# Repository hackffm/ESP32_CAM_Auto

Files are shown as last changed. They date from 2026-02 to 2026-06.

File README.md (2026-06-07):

# ESP32_CAM_Auto
ESP32 Camera FPV Car - some description also on our [Hackerspace-FFM e.V. FPV-Roboter page](https://www.hackerspace-ffm.de/wiki/index.php?title=FPV-Roboter)

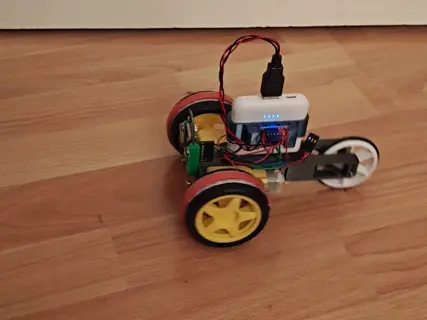
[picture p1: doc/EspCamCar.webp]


# Software setup
## Initial programming of ESP32 CAM Module
Connect it to USB-Serial-Board, hit `Pioarduino -> Project Tasks -> esp32cam -> Custom -> Initial Erase + Flash + FS + Monitor`. 

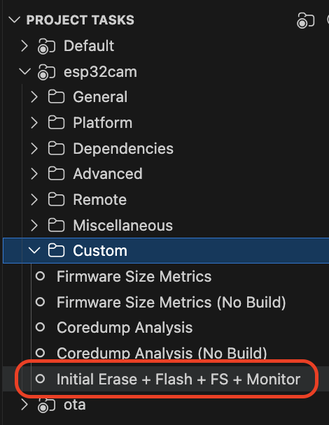
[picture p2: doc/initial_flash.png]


## Architecture infos
- LittleFS is used to store and retrieve WiFi credentials, botname and motor configs. This usually survives a FW update if LittleFS is not uploaded as well. Defaults are used, but LittleFS must be initialized. 
- Camera streams over http port 81 in MJPG mode - this guarantees lowest latency as next frame is only tranferred if current frame was delivered. Usually no significant buffering is used in browsers (this is different for eg RTSP that is why it is not used)
- Code is optimized for OV3660 cameras and support OV2640 cameras. ESP32 CAM boards have known issues with extreme WiFi lag due EMI issues with camera clock signal. We are using the following trick: Reduce external camera clock from 20Mhz to 8Mhz, but then using camera interanl PLL to get same speed again, that way we face much less interference issues.
- http deliveres index.htm and info and action point on port 80. Info streams every second info to browser like fps, but also names for sliders. action is used for controlling everything that is send from browser to the ESP (steering but also settings).
- pwmThing class encapsulates all PWM actions to control LED brightness, set motor speed and servo positions.
- Care must be taken that PWM stuff like analogWrite usually used high-speed timers, but camera clock is using low-speed timers. Arduino does not know about the already used camera timers, but as it uses high-speed timers instead there is no conflict.

# Hardware setup
## Cabling with special PCB
With the special PCB cabling is as easy as connecting left and right motor to the upper 2pin row of the headers and the servo to the lower 3pin row of the headers. For servo, the control line (typical the yellow cable) goes to where the pin is missing on the row above.
If servo does not work, you might need to turn the connector - as long as all 3 pins are connected nothing should broke even if the connector is in the wrong direction. For motor, check that the motors turn forward if you control the joystick forward, otherwise just turn the 2pin connector to change the motor direction of that motor that rotates in the wrong direction.

Supply power from Power Bank via USB-C cable to PCB to turn on the robot. Beware that the PCB does not include the programming hardware for the ESP-CAM - you have to program the ESP-CAM module with a separate programming adapter and then transfer it to the motor driver PCB.

PCB preparation: The idea is that you cut Pin 1 (the one with the square pad on the PCB) away to get a 3+2 pol connector from that originally 2x3 pol connector.
## Manual cabling
- For full-bridge motor drivers connect inputs to 12+13 and 15+14, add connectors to the motors that you can easily swap or turn the motor lines to adjust for correct drive direction
- For 360° servos just pick two of the available pins and set them up via web interface for left and right motor
- We used an USB A plug and a power supply for suppy. In such a case wire separate cables for motors and for ESP32 beginning from USB plug to avoid issues that motor starting currents are affecting ESP32

See the following picture how we did it:

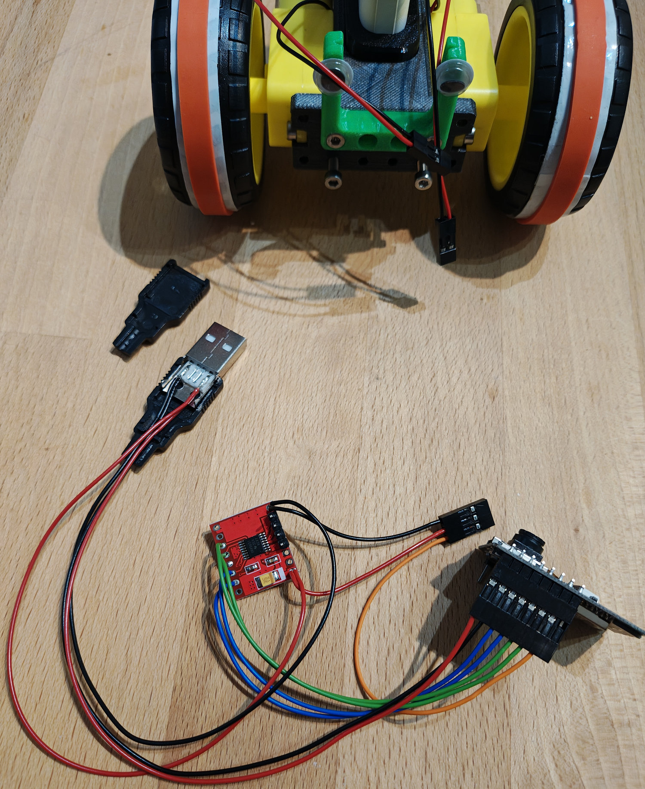
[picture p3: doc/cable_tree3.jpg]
cabling1


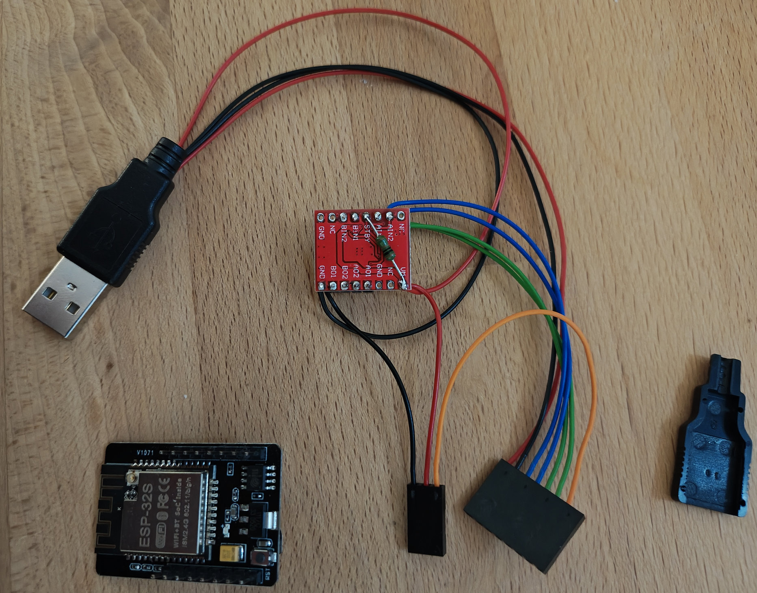
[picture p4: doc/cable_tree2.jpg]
cabling2


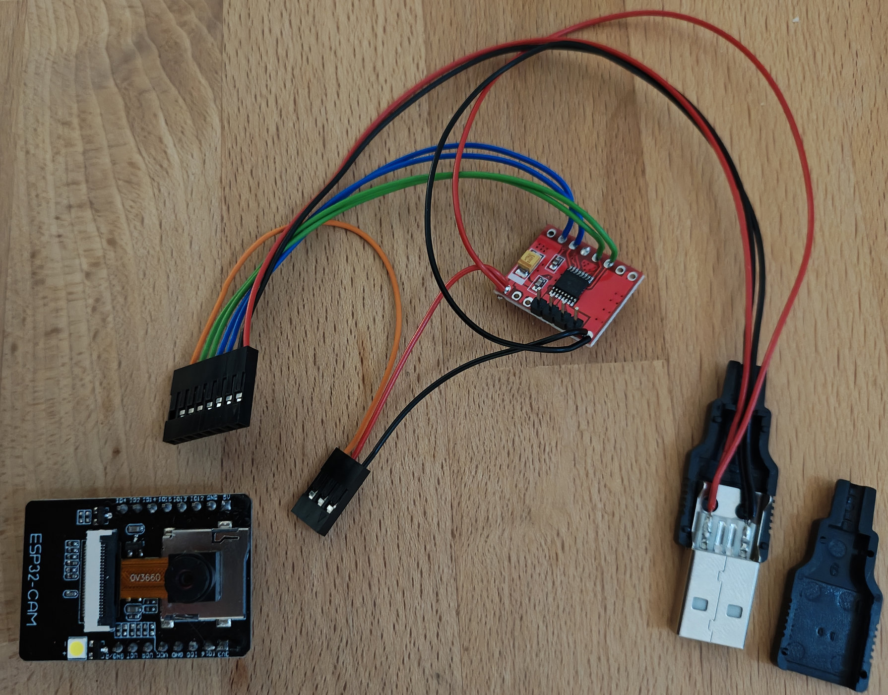
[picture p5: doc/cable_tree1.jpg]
cabling3


## Usable pins
Pins can be redefined via Webinterface but on ESP32 CAM only the following pins are selectable and usable: 
- -1 (if pin or function not needed)
- 2, 12, 13, 14, 15 (free for use, SD card can not be used as these are also for SD card)
- 3 (if used, serial RX is not available anymore)

The following pins can not be used even if they are available on the ESP32 CAM board:
- 0 is used for camera clock signal
- 16 is internally used for PSRAM
- 1 is used for serial TX
- 4 is controlling the white flash LED
- 33 is controlling the red internal LED (might be usable if RedLed PWMThing is connected to pin -1)

## Supported motors
Both servos and full-bridge motor drivers are supported. Currently only seperate left- and right-motor are supported (no steering servo). Servos can then be 360deg servos used as motors, adjust min/zero/max limits for servos, zero is where 360deg servos does not turn (but they are stopped if appropriate servo variant is selected anyway).

# Usage
## LED indications
Slow breathing red LED means normal operation and having a valid WiFi connection. You should be able to control your robot via website of the IP or the name the robot (default: http://cambot.local)

Fast breathing red LED means robot has not found a valid WiFi connection and is acting as WiFi access point. Scan you WiFi environment, connect to the WiFi that matches your robot name (default: cambot), and then go to http://192.168.4.1 to either control your robot directly or connect it to your home WiFi using the Settings area, where you could also scan for your WiFi access points. Beware that the ESP-CAM is 2.4GHz only, so you can connect it only access points that support 2.4GHz WiFi.

No breathing or blinking or off: Something is broken or not powered. If white LED blinks two times the modul could not start the camera module - so check the connection to the camera module first. Beware that to open the camera connector you have to twist the black element by 90° (meaning pulling it away from PCB surface) and not pull it along the PCB. Currently supported camera modules: OV2640 or OV3660 (recommended).

# Known issues
## It does not compile
Uninstall ESP32 core modules in Platform-IO first to force installing newest ones.

### This versions gave a running config
PACKAGES: 
 - contrib-piohome @ 3.4.4 
 - framework-arduinoespressif32 @ 3.3.7 
 - framework-arduinoespressif32-libs @ 5.5.0+sha.87912cd291 
 - tool-esp-rom-elfs @ 2024.10.11 
 - tool-esptoolpy @ 5.1.2 
 - toolchain-xtensa-esp-elf @ 14.2.0+20251107

## Connection issues
- Check Serial output for IP address and if Wifi connection worked.
- Most browsers need at least a slash at the end to not trigger the search engine, try `cambot/`first.
- Name server often have issues, mDNS is also active, try `cambot.local/`if IP can not be resolved.
- Some browsers tries always https, but only http is supported now, try `http://cambot.local`in such case.
- Last resort enter ip address in browser
- If WiFi credentials are not set, either set them via Serial terminal or connect to access point of the device, then open `http://192.168.4.1/`and set there Wifi SSID + password, then power cycle.

## FPS 
Ok, you want the picture as smooth as possible, why limit FPS then? If WiFi is too much congested, everything starts getting sluggy, especially if more than one FPV car is operated it can make sense to limit the frame rate to leave some room for other players. WiFi at 2.4 GHz can transmit around 3,000 kBytes/s (but an ESP32 max out usually already at 1,000 kBytes/s due internal limits), depending on quality settings and picture size we integrated at least 4 fpv cars in the band without issues simultaneously. Keep an eye on RSSI, if it falls below -70 dBm the WiFi bandwith starts to be limited significantly affecting also the frame rate of that vehicle.  

## Camera overheating
Especially the OV3660 moduls are working on ESP32 CAM boards, but are operated out of voltage specifications there. Therefore they are more prone to heat up - glue them with thin double sided tape to the SD card holder to give them a little more cooling surface. Camera is specified to operate with best picture quality up to 50°C, they are specified to allow operation up to 70°C, we see it often a little bit higher than that but it seems to be ok. As said, issue is that OV2640 is usually prefered over OV3660 du to better picture and speed but are more prone to overheating.

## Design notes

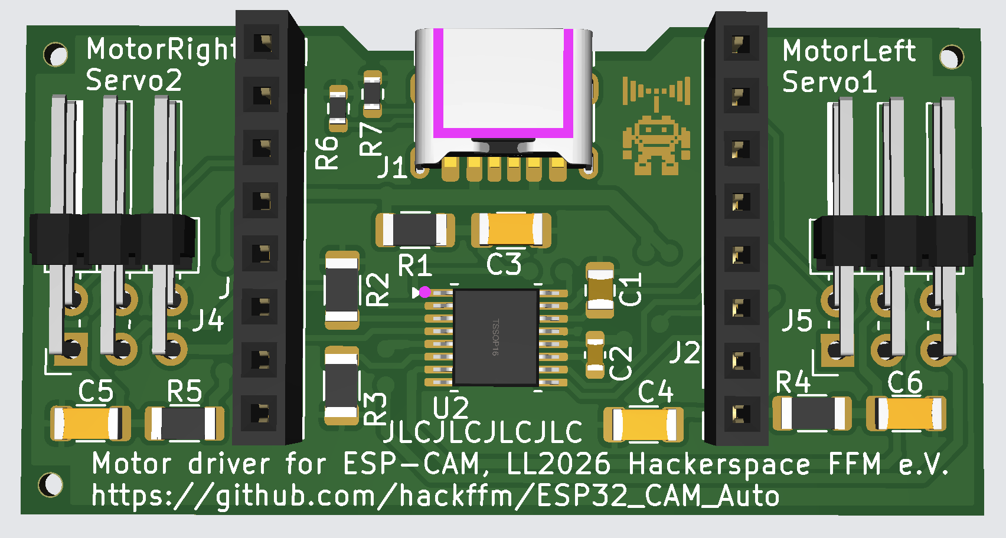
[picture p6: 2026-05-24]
pcb/docu/Motor driver for ESP-CAM PCB 3D.png

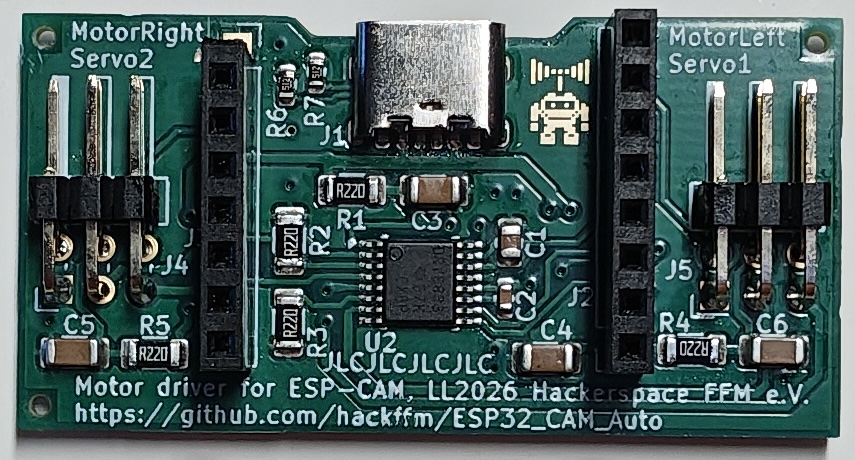
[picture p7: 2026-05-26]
pcb/docu/Motor driver PCB delivered and pins cut.jpg

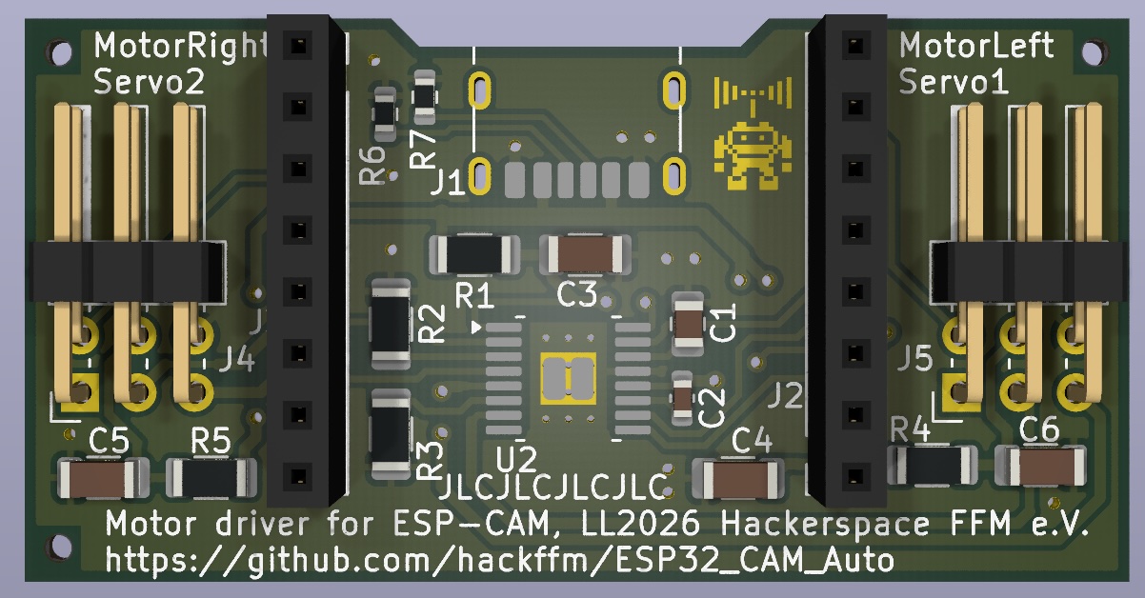
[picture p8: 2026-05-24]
pcb/docu/Motor driver for ESP-CAM KiCadRendering.jpg

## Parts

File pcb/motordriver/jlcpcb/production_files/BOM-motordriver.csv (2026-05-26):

Comment | Designator | Footprint | LCSC | Quantity
0.01uF | C2 | C_0603_1608Metric | C57112 | 1
0.22R | R1,R2,R3,R4,R5 | R_1206_3216Metric | C327006 | 5
2.2uF | C1 | C_0805_2012Metric | C377773 | 1
22uF | C3,C4,C5,C6 | C_1206_3216Metric | C12891 | 4
5k1 | R6,R7 | R_0603_1608Metric | C23186 | 2
Conn_01x08_Pin | J2,J3 | PinSocket_1x08_P2.54mm_Vertical | C22438158 | 2
Conn_02x03_Odd_Even | J4,J5 | PinHeader_2x03_P2.54mm_Horizontal | C492431 | 2
DRV8833PWP | U2 | HTSSOP-16-1EP_4.4x5mm_P0.65mm_EP3.4x5mm_Mask2.46x2.31mm_ThermalVias | C50506 | 1
USB_C_Receptacle_PowerOnly_6P | J1 | USB_C_Receptacle_HRO_TYPE-C-31-M-17 | C283540 | 1
~ | H3 | Hole_Tooling_JLCPCB |  | 1
~ | H2 | Hole_Tooling_JLCPCB |  | 1
~ | H1 | Hole_Tooling_JLCPCB |  | 1
~ | PN1 | Part_Num_JLCPCB |  | 1

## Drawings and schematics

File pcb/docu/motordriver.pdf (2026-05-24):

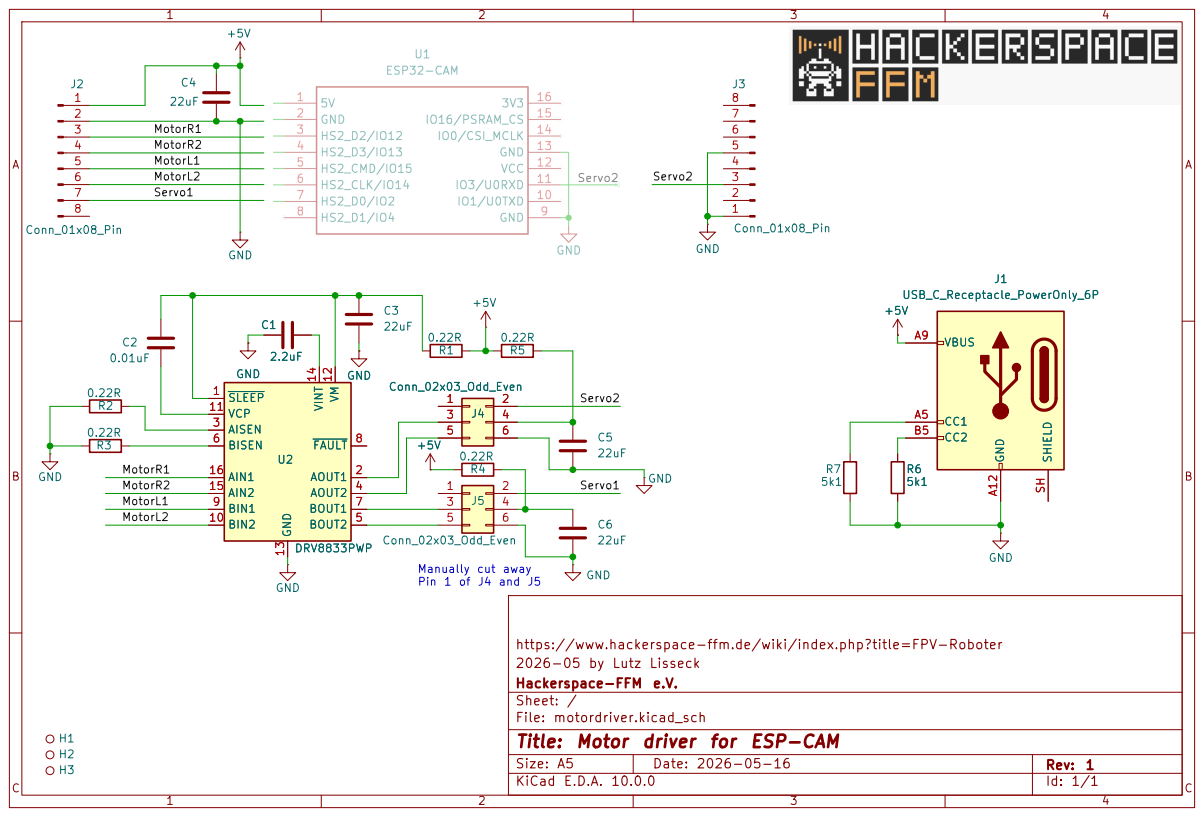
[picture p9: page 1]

Servo1 Manually cut away Pin 1 of J4 and J5 +5V

Sheet: /
File: motordriver.kicad_sch
Title: Motor driver for ESP-CAM

Size: A5 | Rev: 1 | C Date: 2026-05-16 KiCad E.D.A. 10.0.0

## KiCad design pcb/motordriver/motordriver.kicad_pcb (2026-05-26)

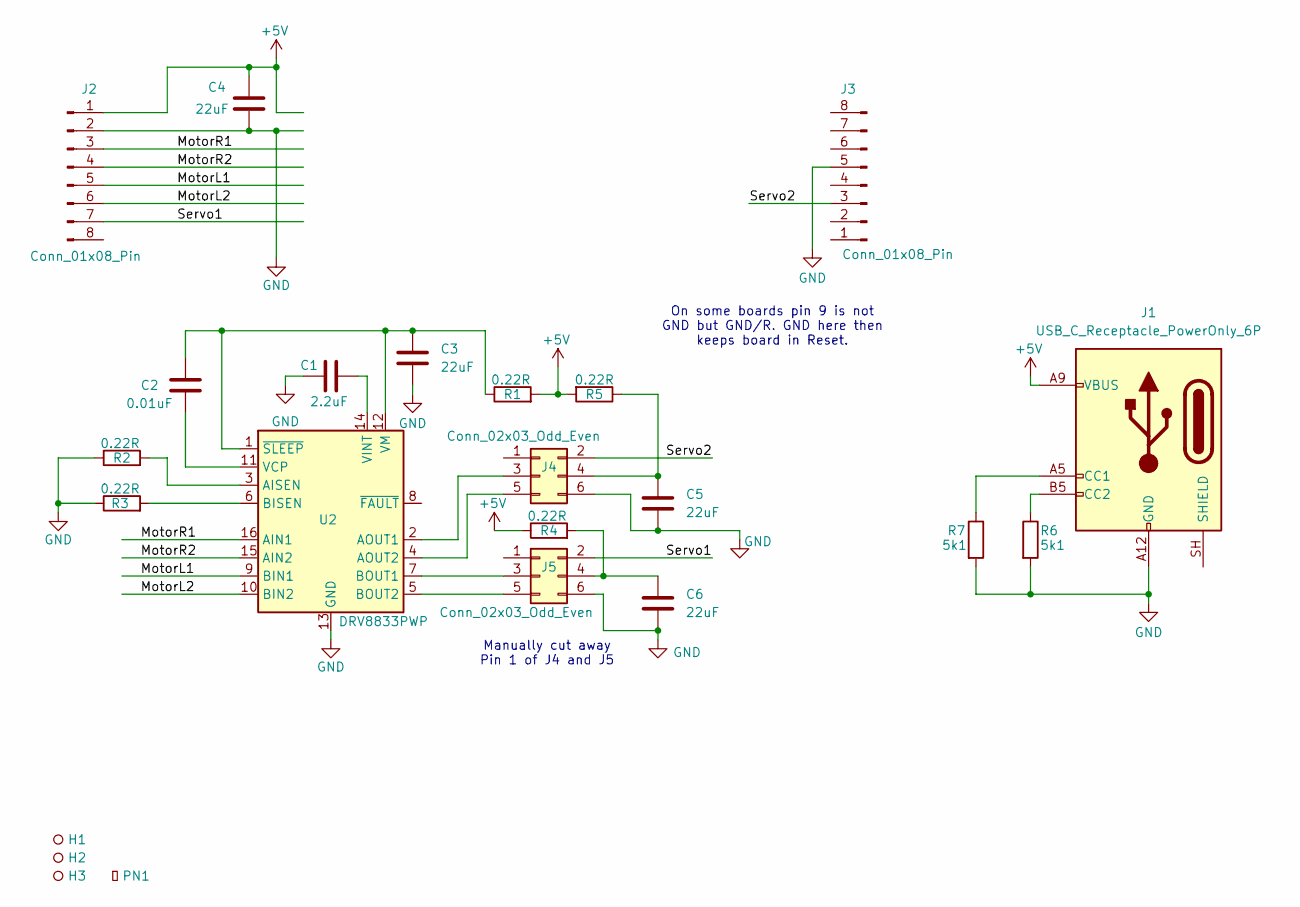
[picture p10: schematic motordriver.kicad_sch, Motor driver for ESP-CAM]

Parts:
C1: 2.2uF; C_0805_2012Metric; LCSC C377773
C2: 0.01uF; C_0603_1608Metric; LCSC C57112
C3, C4, C5, C6: 22uF; C_1206_3216Metric; LCSC C12891
H1, H2, H3: Hole_Tooling_JLCPCB
J1: USB_C_Receptacle_PowerOnly_6P; USB_C_Receptacle_HRO_TYPE-C-31-M-17; LCSC C283540
J2, J3: Conn_01x08_Pin; PinSocket_1x08_P2.54mm_Vertical; LCSC C22438158
J4, J5: Conn_02x03_Odd_Even; PinHeader_2x03_P2.54mm_Horizontal; LCSC C492431
PN1: Part_Num_JLCPCB
R1, R2, R3, R4, R5: 0.22R; R_1206_3216Metric; LCSC C327006
R6, R7: 5k1; R_0603_1608Metric; LCSC C23186
U2: DRV8833PWP; HTSSOP-16-1EP_4.4x5mm_P0.65mm_EP3.4x5mm_Mask2.46x2.31mm_The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; LCSC C50506

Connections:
+5V: C4.2, J1.A9 (VBUS), J1.B9 (VBUS), J2.1, R1.2, R4.1, R5.2
/MotorL1: J2.5, U2.9 (BIN1)
/MotorL2: J2.6, U2.10 (BIN2)
/MotorR1: J2.3, U2.16 (AIN1)
/MotorR2: J2.4, U2.15 (AIN2)
/Servo1: J2.7, J5.2
/Servo2: J3.3, J4.2
GND: C1.1, C3.2, C4.1, C5.2, C6.2, J1.A12 (GND), J1.B12 (GND), J2.2, J3.5, J4.6, J5.6, R2.1, R3.1, R6.2, R7.2, U2.13 (GND), U2.17 (GND)
unnamed: J1.A5 (CC1), R7.1
unnamed: J1.B5 (CC2), R6.1
unnamed: J4.3, U2.2 (AOUT1)
unnamed: C5.1, J4.4, R5.1
unnamed: J4.5, U2.4 (AOUT2)
unnamed: J5.3, U2.7 (BOUT1)
unnamed: C6.1, J5.4, R4.2
unnamed: J5.5, U2.5 (BOUT2)
unnamed: R2.2, U2.3 (AISEN)
unnamed: R3.2, U2.6 (BISEN)
unnamed: C2.2, U2.11 (VCP)
unnamed: C1.2, U2.14 (VINT)
unnamed: C2.1, C3.1, R1.1, U2.1 (~SLEEP), U2.12 (VM)

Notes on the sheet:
Manually cut away Pin 1 of J4 and J5
On some boards pin 9 is not GND but GND/R. GND here then keeps board in Reset.

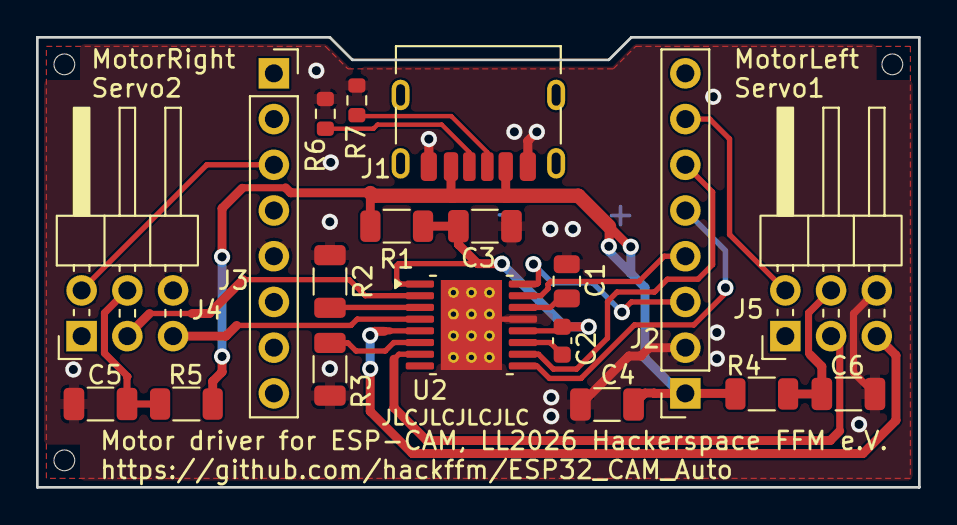
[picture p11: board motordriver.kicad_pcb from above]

Board: 2 copper layers, 49.0 x 25.0 mm, 23 parts (0 on the bottom side), 21 nets.

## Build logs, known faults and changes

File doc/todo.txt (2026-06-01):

Webseite:
  - SSID (Wlan-Name hinterschreiben weil leute SSID nicht wissen)
  - Übernamhme der Daten mit Reboot wurde nicht verstanden 
    - wie drücken oder ab- neu anstecken
  - Servo-Button ins Bild
  - Controller Settings speichern (im Browser speichern)
  - Manuelle Controller Auswahl broken
  - 7fps muss weg 
  - Bild 180 drehen

Anleitung:
  - Wie Wifi Einstellungen prüfen (Verbindung geht oder noch im AP Modus)
  - Hinweis das Wifi-Passwort aufs Handy zu übertragen bevor auf den Bot-AP gewechselt wird
  - 5Ghz only geht nicht  
  
Wifi:
  - Captive Portal Seite ging nicht (WLED checken)
  - Erkannte APs zur Auswahl anzeigen

Auto-Power-Down nach Inaktivität

FW Update

Extra Einstellungen:
- Bild 180 drehen
-

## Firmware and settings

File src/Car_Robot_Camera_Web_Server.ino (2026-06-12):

/*********
 
   The MIT License (MIT) 
   Hackerspace-FFM e.V. ESP32 CAM Robot with Web Interface
   https://www.hackerspace-ffm.de/wiki/index.php?title=FPV-Roboter
   2026-06-12 Lutz Lisseck 

  Derived from this work: 
  Rui Santos & Sara Santos - Random Nerd Tutorials
  Complete instructions at https://RandomNerdTutorials.com/esp32-cam-projects-ebook/
  Permission is hereby granted, free of charge, to any person obtaining a copy of this software and associated documentation files.
  The above copyright notice and this permission notice shall be included in all copies or substantial portions of the Software.
*********/

const char version_string[] = "V1.14";

#define MOTOR_1_PIN_1    14
#define MOTOR_1_PIN_2    15
#define MOTOR_2_PIN_1    13
#define MOTOR_2_PIN_2    12
#define SERVO_1_PIN       2
#define WHITE_LED_PIN     4
#define RED_LED_PIN      33

// Wifi credentials are in a MyCreds.h file that must reside in /<HOME>/.platformio/lib/MyCreds/MyCreds.h
// see attic/MyCreds.h for an example
#if defined __has_include
#  if __has_include (<MyCredsLabyrinth.h>)
#    include <MyCredsLabyrinth.h>  // Define WIFI_SSID and WIFI_PASSWORD here - put this file in /<HOME>/.platformio/lib/MyCreds/MyCredsHackffm.h
#  else
#    define WIFI_SSID ""
#    define WIFI_PASSWORD ""
#  endif
#else
#  define WIFI_SSID ""
#  define WIFI_PASSWORD ""
#endif

// Replace with your network credentials, will be overwritten by values stored in LittleFS if available
char roboter_name[34] = "cambot"; // only use a-z, 0-9 and - in the name 
char wifi_ssid[34] = WIFI_SSID;  // "REPLACE_WITH_YOUR_SSID";
char wifi_password[66] = WIFI_PASSWORD; // "REPLACE_WITH_YOUR_PASSWORD";

// =============================================================
//  User-configurable channel list for scanning.
//  Fill this with the channels you actually want to probe.
//  Using non-overlapping channels (e.g. 1, 6, 11 or 1, 7, 13)
//  keeps the scan short and the stream interruption minimal.
//  Leave empty {} to scan ALL channels (slower).
// =============================================================
static const uint8_t ROAM_SCAN_CHANNELS[] = {}; //{1,2,3,4,5,6,7,8,9,10,11,12,13}; // { 1, 7, 13 };
static const size_t  ROAM_SCAN_CHANNEL_COUNT =
        sizeof(ROAM_SCAN_CHANNELS) / sizeof(ROAM_SCAN_CHANNELS[0]);

#include "esp_camera.h"
#include <WiFi.h>
#include "esp_wifi.h"
#include <WiFiMulti.h>
#include <WiFiUdp.h>
#include <lwip/sockets.h>
#include <lwip/netdb.h>
#include <DNSServer.h> // For captive portal
#include <ESPmDNS.h>
#include "esp_timer.h"
#include "img_converters.h"
#include "Arduino.h"
#include "fb_gfx.h"
#include "soc/soc.h"             // disable brownout problems
#include "soc/rtc_cntl_reg.h"    // disable brownout problems
#include "esp_http_server.h"
#include "driver/ledc.h" 
#include <ArduinoOTA.h>
#include "PwmThing.h"
#include "FS.h"
#include <LittleFS.h> 
#include <string.h>
#include <stdlib.h>
#include <ctype.h>

// =============================================================
//  Detect whether 802.11r Fast Transition is compiled into
//  this build. This is decided at compile time.
// =============================================================
#ifdef CONFIG_ESP_WIFI_11R_SUPPORT
  #define ROAM_FT_AVAILABLE 1
#else
  #define ROAM_FT_AVAILABLE 0
#endif

#define ENABLE_OTA 
int OTA_Status = 0; // 0=not enabled, 1=enabled, 2=in progress
DNSServer dnsServer;
bool APMode = false;
bool RoamForceTriggered = false;


IPAddress current_IP(192, 168, 4, 1);
char      current_ssid[34] = ""; 
char      current_bssid[34] = ""; 
int       current_channel = 0;
int       current_rssi = -50;

PwmThing MotorLeft, MotorRight, Servo1, Servo2, WhiteLED, RedLED;

WiFiMulti wifiMulti;

// Gamemaster stuff
const unsigned int gmPort = 8071;        // UDP port for gamemaster
IPAddress gmLastRemoteIp;
uint16_t  gmLastRemotePort = 0;
bool      gmLastRemoteValid = false;
WiFiUDP gmUdp;

// Store data used in PwmThing.begin for Motors and Servos here in an array of a structto be stored in LittleFS and to be used on startup
struct PwmThingConfig {
  char name[20]; int pinA; int pinB; PwmThing::ThingType thingType; bool inverted;
  int servoMin; int servoZero; int servoMax; /* Only for servos*/
};

// Create an array of PwmThingConfig for the motors and servos and populate it with default values
const int numPwmThings = 4;
PwmThingConfig pwmThingConfigs[numPwmThings] = {
  {"MotorLeft", MOTOR_1_PIN_1, MOTOR_1_PIN_2, PwmThing::halfBridgeIdleHigh, false, 768, 4760, 9544},
  {"MotorRight", MOTOR_2_PIN_1, MOTOR_2_PIN_2, PwmThing::halfBridgeIdleHigh, false, 768, 4760, 9544},
  {"Servo1", SERVO_1_PIN, -1, PwmThing::servoMotor, false, 768, 4760, 9544},
  {"Servo2", -1, -1, PwmThing::servoMotor, false, 768, 4760, 9544}
};

uint32_t lastMotorCommandTime = 0;
uint32_t powerDownTimer = 0;
uint32_t powerDownTimeout = 60 * 60000UL; // Power down 30 min

struct LightVariables {
  // All values are usually 0...255 for 0% to 100% brightness
  int requestedValue = -1;          // User request goes here, -1 means no request, applied in main loop with limits and timeouts
  int Value = 0;                    // What the light is currently set to, timeouts and limits are applied to this value, and this is what is actually set on the LED
  int lowValue = 50;                // User defined value for candle/torch light (no time limit if below limitLowValue)
  int highValue = 255;              // User defined value for strong brightness (will be time limited)
  int limitLowValue = 75;           // Unlimited brightness up to this value, above this value, the timeout will apply
  int limitHighValue = 250;         // Absolute maximum allowed brightness, even for boost, to prevent overheating
  int boostTime = 30000;            // Available boost time in milliseconds
  int boostTimeMax = 30000;         // Maximum boost time in milliseconds (e.g. to calculate remaining boost time percentage)
} LightVars;

struct ServoVariables {
  // All values -255 ... 255 typically (percentage of PwmThing ServoMin and ServoMax)
  int requestedValue = -9999;    // User request goes here, -9999 means no request, applied in main loop with limits and timeouts
  int Value = 0;                 // What the servo is currently set to
  int lowValue = -30;            // User defined value for one lower position 
  int highValue = 150;           // User defined value for one higher position
} Servo1Vars, Servo2Vars;

#define CAMERA_MODEL_AI_THINKER
//#define CAMERA_MODEL_M5STACK_PSRAM
//#define CAMERA_MODEL_M5STACK_WITHOUT_PSRAM
//#define CAMERA_MODEL_M5STACK_PSRAM_B
//#define CAMERA_MODEL_WROVER_KIT

#include "cam_pindefs.h"
#include "cam_streamhandler.h"
#include "indexhtml_intern.h"  // will be replaced if /data/index.html in LittleFS exists
#include "settingshtml_intern.h"  // will be replaced if /data/settings.html in LittleFS exists

#include "helper_functions.h"

struct CameraConfig {
  int rotation; // 0 = no rotation, 1 = 180° rotation
  int size; // 0 = 320x240 (QVGA), 1 = 400x296 (CIF), 2 = 640x480 (VGA), 3 = 800x600 (SVGA), 4 = 1024x768 (XGA), 5 = 1280x1024 (SXGA), 6 = 1600x1200 (UXGA)
  int fps; // Limit FPS, 0 = auto, 1...7 = 2,5,10,15,20,25,30 fps
  int quality; // 0 = auto, 1 very poor (63), 2 poor (42), 3 medium (30), 4 good (18), 5 very good (6)
} cameraConfig = {0, 2, 0, 0};
// current values go to quality and frame_limit_ms in cam_streamhandler.h, they are updated from there when changed 

fs::FS &filesystem = LittleFS;

void setCameraToConfig() {
  sensor_t * s = esp_camera_sensor_get();
  framesize_t size2framesize[] = {FRAMESIZE_QVGA, FRAMESIZE_CIF, FRAMESIZE_VGA, FRAMESIZE_SVGA, 
    FRAMESIZE_XGA, FRAMESIZE_SXGA, FRAMESIZE_UXGA};
  if(cameraConfig.size < 0 || cameraConfig.size > 6) cameraConfig.size = 2; // default to VGA if out of bounds  
  s->set_framesize(s, size2framesize[cameraConfig.size]);
  //s->set_quality(s, cameraConfig.quality);

  int fps_values[] = {15, 2, 5, 10, 15, 20, 25, 30};
  if(cameraConfig.fps < 0 || cameraConfig.fps > 7) cameraConfig.fps = 0; // default to auto if out of bounds
  int fps_value = fps_values[cameraConfig.fps];
  frame_limit_ms = fps_value > 0 ? 1000 / fps_value : 0; // 0 means no limit

  int quality_values[] = {33, 63, 42, 30, 18, 6}; // Map 0...5 to quality values (0=auto, 1=very poor, ..., 5=very good)
  if(cameraConfig.quality < 0 || cameraConfig.quality > 5) cameraConfig.quality = 0; // default to auto if out of bounds
  quality = quality_values[cameraConfig.quality];

  camera_sensor_info_t *info = esp_camera_sensor_get_info(&s->id);

  if((info->model == CAMERA_OV3660)) {
    if(cameraConfig.rotation == 1) {
      s->set_hmirror(s, 0);
      s->set_vflip(s, 1);
    } else {
      s->set_hmirror(s, 1);
      s->set_vflip(s, 0);
    }
    //s->set_xclk(s, LEDC_TIMER_0, 8000000UL);
    s->set_pll(s, 0, 25, 1, 0, 0, 0, 1, 10); // pushes 8MHz ext to same internally as 20mhz before
    s->set_reg(s, 0x302c, 0xc0, 0x00); // Reduce pad driving strength for better EMI/radio 
    s->set_reg(s, 0x6706, 0x0f, 0x03); // Adjust temperature sampling frequency to 8 MHz XVCLK
    // s->set_brightness(s, 0); // Increase brightness to reduce noise in dark areas
    //s->set_raw_gma(s, 1); s->set_reg(s, 0x5480, 1, 0);
    //s->set_gainceiling(s, GAINCEILING_32X);
  } else if(s->id.PID == OV2640_PID) {
    if(cameraConfig.rotation == 1) {
      s->set_hmirror(s, 1);
      s->set_vflip(s, 1);
    } else {
      s->set_hmirror(s, 0);
      s->set_vflip(s, 0);
    }
    s->set_gainceiling(s, (gainceiling_t)2); // default is 2x, set to 1x to reduce noise
    s->set_reg(s, 0x111, 0xff, 0x80); // activae clock doubler to compensate 8 Mhz 
  }

}

void storeCameraConfig() {
  char buffer[50];
  snprintf(buffer, sizeof(buffer), "%d,%d,%d,%d\n", cameraConfig.rotation, cameraConfig.size, cameraConfig.fps, cameraConfig.quality);
  writeFile("/camera_config.txt", buffer);
}

void loadCameraConfig() {
  char buffer[50];
  if(filesystem.exists("/camera_config.txt")) {
    File file = filesystem.open("/camera_config.txt", "r");
    if(file) {
      size_t len = file.readBytes(buffer, sizeof(buffer)-1);
      buffer[len] = '\0';
      sscanf(buffer, "%d,%d,%d,%d", &cameraConfig.rotation, &cameraConfig.size, &cameraConfig.fps, &cameraConfig.quality);
      file.close();
    }
  }
}

void initPwmThings() {
    // Disable UART RX if pinA or pinB is using GPIO3
    if(pwmThingConfigs[0].pinA == 3 || pwmThingConfigs[0].pinB == 3 || 
       pwmThingConfigs[1].pinA == 3 || pwmThingConfigs[1].pinB == 3 || 
       pwmThingConfigs[2].pinA == 3 || pwmThingConfigs[2].pinB == 3 || 
       pwmThingConfigs[3].pinA == 3 || pwmThingConfigs[3].pinB == 3) {
      Serial.println("Disabling UART RX because GPIO3 is used for IO.");
      delay(100); Serial.end();
      Serial.begin(115200, SERIAL_8N1, -1); // Disable RX pin by setting it to -1
    }
    MotorLeft.begin(pwmThingConfigs[0].pinA, pwmThingConfigs[0].pinB, pwmThingConfigs[0].thingType, pwmThingConfigs[0].inverted, 
      pwmThingConfigs[0].servoMin, pwmThingConfigs[0].servoZero, pwmThingConfigs[0].servoMax);
    MotorRight.begin(pwmThingConfigs[1].pinA, pwmThingConfigs[1].pinB, pwmThingConfigs[1].thingType, pwmThingConfigs[1].inverted,
      pwmThingConfigs[1].servoMin, pwmThingConfigs[1].servoZero, pwmThingConfigs[1].servoMax);
    Servo1.begin(pwmThingConfigs[2].pinA, pwmThingConfigs[2].pinB, pwmThingConfigs[2].thingType, pwmThingConfigs[2].inverted,
      pwmThingConfigs[2].servoMin, pwmThingConfigs[2].servoZero, pwmThingConfigs[2].servoMax);
    Servo2.begin(pwmThingConfigs[3].pinA, pwmThingConfigs[3].pinB, pwmThingConfigs[3].thingType, pwmThingConfigs[3].inverted,
      pwmThingConfigs[3].servoMin, pwmThingConfigs[3].servoZero, pwmThingConfigs[3].servoMax);
}

void storePwmThingConfigs() {
  char filename[30];
  char buffer[256];
  for(int i=0; i<numPwmThings; i++) {
    snprintf(filename, sizeof(filename), "/%s.txt", pwmThingConfigs[i].name);
    snprintf(buffer, sizeof(buffer), "%d,%d,%d,%d,%d,%d,%d\n", 
      pwmThingConfigs[i].pinA, pwmThingConfigs[i].pinB, (int)pwmThingConfigs[i].thingType, (int)pwmThingConfigs[i].inverted,
      pwmThingConfigs[i].servoMin, pwmThingConfigs[i].servoZero, pwmThingConfigs[i].servoMax);
    writeFile(filename, buffer);
  }
}

void loadPwmThingConfigs() {
  char filename[30];
  char buffer[256];
  for(int i=0; i<numPwmThings; i++) {
    snprintf(filename, sizeof(filename), "/%s.txt", pwmThingConfigs[i].name);
    if(filesystem.exists(filename)) {
      File file = filesystem.open(filename, "r");
      if(file) {
        size_t len = file.readBytes(buffer, sizeof(buffer)-1);
        buffer[len] = '\0';
        sscanf(buffer, "%d,%d,%d,%d,%d,%d,%d", 
          &pwmThingConfigs[i].pinA, &pwmThingConfigs[i].pinB, (int*)&pwmThingConfigs[i].thingType, (int*)&pwmThingConfigs[i].inverted,
          &pwmThingConfigs[i].servoMin, &pwmThingConfigs[i].servoZero, &pwmThingConfigs[i].servoMax);
        file.close();
      }
    }
  }
}

void loadLightServoLowHighVals() {
  char buffer[50];
  if(filesystem.exists("/ls_lh_vals.txt")) {
    File file = filesystem.open("/ls_lh_vals.txt", "r");
    if(file) {
      size_t len = file.readBytes(buffer, sizeof(buffer)-1);
      buffer[len] = '\0';
      sscanf(buffer, "%d,%d,%d,%d,%d,%d", &LightVars.lowValue, &LightVars.highValue, &Servo1Vars.lowValue, &Servo1Vars.highValue, &Servo2Vars.lowValue, &Servo2Vars.highValue);
      file.close();
    }
  }
}

void storeLightServoLowHighVals() {
  char buffer[50];
  snprintf(buffer, sizeof(buffer), "%d,%d,%d,%d,%d,%d\n", LightVars.lowValue, LightVars.highValue, Servo1Vars.lowValue, Servo1Vars.highValue, Servo2Vars.lowValue, Servo2Vars.highValue);
  writeFile("/ls_lh_vals.txt", buffer);
}

httpd_handle_t camera_httpd = NULL;
httpd_handle_t stream_httpd = NULL;

static esp_err_t index_handler(httpd_req_t *req)
{
  Serial.printf("Handling request for %s\n", req->uri);

  char filename[32] = {0,};
  const char *pData = NULL;
  size_t dataLen = 0;
  const char req_type[32] = "text/html";

  if(strcmp(req->uri, "/") == 0 || strcmp(req->uri, "/index.html") == 0) {
    strcpy(filename, "/index.html");
    pData = INDEX_HTML;
    dataLen = strlen(INDEX_HTML);
  } else if (strcmp(req->uri, "/settings") == 0 || strcmp(req->uri, "/settings.html") == 0) {
    strcpy(filename, "/settings.html");
    pData = SETTINGS_HTML;
    dataLen = strlen(SETTINGS_HTML);
  } else if (strcmp(req->uri, "/favicon.ico") == 0) {
    httpd_resp_set_type(req, "image/x-icon");
    return httpd_resp_send(req, (const char *)favicon, sizeof(favicon));
  } 

  if(filesystem.exists(filename) == false) {
    Serial.printf("Serving internal %s\n", filename);
    httpd_resp_set_type(req, req_type);
    return httpd_resp_send(req, pData, dataLen);  
  } 
  Serial.printf("Serving external %s from LittleFS\n", filename);
  File file = filesystem.open(filename, "r");
  if (!file) {
      httpd_resp_send_404(req);
      Serial.printf("Failed to open file %s\n", filename);
      return ESP_FAIL;
  }
  httpd_resp_set_type(req, req_type);

  char chunk[1024];
  size_t read_bytes;
  while((read_bytes = file.readBytes(chunk, sizeof(chunk))) > 0) {
  //  Serial.printf("Read %d bytes from file\n", read_bytes);
    if (httpd_resp_send_chunk(req, chunk, read_bytes) != ESP_OK) {
      file.close();
      httpd_resp_sendstr_chunk(req, NULL); // end response
      return ESP_FAIL;
    }
  }
  file.close();
  httpd_resp_send_chunk(req, NULL, 0);
  return ESP_OK;
}

char infotext[256] = "";

static esp_err_t info_handler(httpd_req_t *req){
  static char info[2048];
  int info_len = 0;
  // sprintf(infotext, "BSSID: %s, Camera: %s", WiFi.BSSIDstr().c_str(), info->name);
  info_len = snprintf(info, sizeof(info), "%s, Cam-Temp: %d°C, Free heap: %u, Free PSRAM: %u, \r\n", 
     infotext, camera_temp, ESP.getFreeHeap(), ESP.getFreePsram());
  info_len += snprintf(info + info_len, sizeof(info) - info_len, "SSID: %s, BSSID: %s, IP: %s \r\n", 
     current_ssid, current_bssid,  current_IP.toString().c_str());
  info_len += snprintf(info + info_len, sizeof(info) - info_len, "Avg RSSI: %d dBm, FPS: %d/%d, Quality: %d, kBytes/s: %d, Command/s: %d\r\n", 
     current_rssi, fps, frame_limit_ms?1000/frame_limit_ms:0, quality, bps/1024, cps);    
  info_len += snprintf(info + info_len, sizeof(info) - info_len, "ML: %d, MR: %d, Powerdown timer: %lu s\r\n", 
     MotorLeft.get(), MotorRight.get(), (powerDownTimeout - (millis() - powerDownTimer))/1000);      
  info_len += snprintf(info + info_len, sizeof(info) - info_len, "Version: %s %s, Uptime: %lu s\r\n", version_string, CompileTime, millis() / 1000);  
  info_len += snprintf(info + info_len, sizeof(info) - info_len, "| Name=\"%s\", A=\"FPS-Limit (%d fps)\", "
     "B=\"Quality (%d)\", C=\"LED (Boost remaining: %ds)\", D=\"Servo1 (%d)\", E=\"Servo2 (%d)\", ", 
     roboter_name, frame_limit_ms?1000/frame_limit_ms:0, quality, LightVars.boostTime/1000,0, Servo1.getDuty(), Servo2.getDuty());
  info_len += snprintf(info + info_len, sizeof(info) - info_len, "lightValue=\"%d\", lightLowValue=\"%d\", lightHighValue=\"%d\", "
      "lightLimitLowValue=\"%d\", lightLimitHighValue=\"%d\", lightBoostTime=\"%d\", lightBoostTimeMax=\"%d\", ", 
     LightVars.Value, LightVars.lowValue, LightVars.highValue, LightVars.limitLowValue, LightVars.limitHighValue, 
     LightVars.boostTime/1000, LightVars.boostTimeMax/1000);   
  info_len += snprintf(info + info_len, sizeof(info) - info_len, "Servo1Value=\"%d\", Servo1LowValue=\"%d\", Servo1HighValue=\"%d\", " 
      "Servo1RawValue=\"%d\", Servo2Value=\"%d\", Servo2LowValue=\"%d\", Servo2HighValue=\"%d\", Servo2RawValue=\"%d\", ",
     Servo1Vars.Value, Servo1Vars.lowValue, Servo1Vars.highValue, Servo1.getDuty(), 
     Servo2Vars.Value, Servo2Vars.lowValue, Servo2Vars.highValue, Servo2.getDuty());
  info_len += snprintf(info + info_len, sizeof(info) - info_len, "Version=\"%s\", ", version_string);

  char status[255] = "FPS: 12/30, Q:32, RSSI:-75";
  snprintf(status, sizeof(status), "FPS:%d/%d, Q:%d, RSSI:%d, Ch:%d", fps, frame_limit_ms?1000/frame_limit_ms:0, 
     quality, current_rssi, current_channel);
  info_len += snprintf(info + info_len, sizeof(info) - info_len, "Status=\"%s\", ", status);
  httpd_resp_set_type(req, "text/plain");
  return httpd_resp_send(req, info, strlen(info));
}

static esp_err_t cors_options_handler(httpd_req_t *req) {
    httpd_resp_set_hdr(req, "Access-Control-Allow-Origin", "*");
    httpd_resp_set_hdr(req, "Access-Control-Allow-Methods", "GET, OPTIONS");
    httpd_resp_set_hdr(req, "Access-Control-Allow-Headers", "*");
    httpd_resp_send(req, NULL, 0);    // 204 No Content
    return ESP_OK;
}

// HTTP Error (404) Handler - Redirects all requests to the root page
static esp_err_t http_404_error_handler(httpd_req_t *req, httpd_err_code_t err) {
    httpd_resp_set_status(req, "303 See Other"); // Set status
    httpd_resp_set_hdr(req, "Location", "/"); // Redirect to the "/" root directory
    // iOS requires content in the response to detect a captive portal, simply redirecting is not sufficient.
    httpd_resp_send(req, "Redirect to the captive portal", HTTPD_RESP_USE_STRLEN);
    ESP_LOGI(TAG, "Redirecting to root");
    return ESP_OK;
}
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
void loop() {
  if(OTA_Status < 2) {
    calc_fps();
    adjust_to_rssi();
  }

  #ifdef ENABLE_OTA
  ArduinoOTA.handle(); // allow OTA updates
  #endif

  if(APMode) dnsServer.processNextRequest(); // Handle DNS requests in AP mode for captive portal

  RedLED.doAnimation();
  adjust_light();

  static uint32_t limitServoUpdate = millis();
  if(millis() - limitServoUpdate > 40) {
    limitServoUpdate = millis();
    Servo1.doAnimation();
  }

  if(lastMotorCommandTime > 0 && (millis() - lastMotorCommandTime > 3000)) {
    MotorLeft.set(0);
    MotorRight.set(0);
    lastMotorCommandTime = 0;
    Serial.println("Motor command timeout, stopping motors");
  }

  // Auto power down
  if(lastMotorCommandTime == 0) {
    if((powerDownTimeout > 0) && (millis() - powerDownTimer > powerDownTimeout)) {
      powerDown();
    }
  } else {
    powerDownTimer = millis(); // Reset power down timer when motor command is active
  }
  if(powerDownTimeout == 0xfffffffful) { powerDown();}

  processSerial(); // Check for serial commands 
  handleGmUdp();

  if(!APMode) {
    wifiRoamTask(RoamForceTriggered); // Check if we should roam to a better AP
    RoamForceTriggered = false; // Reset roam trigger after handling
  }

  delay(10);
}

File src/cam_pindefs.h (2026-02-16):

#if defined(CAMERA_MODEL_WROVER_KIT)
  #define PWDN_GPIO_NUM    -1
  #define RESET_GPIO_NUM   -1
  #define XCLK_GPIO_NUM    21
  #define SIOD_GPIO_NUM    26
  #define SIOC_GPIO_NUM    27
  
  #define Y9_GPIO_NUM      35
  #define Y8_GPIO_NUM      34
  #define Y7_GPIO_NUM      39
  #define Y6_GPIO_NUM      36
  #define Y5_GPIO_NUM      19
  #define Y4_GPIO_NUM      18
  #define Y3_GPIO_NUM       5
  #define Y2_GPIO_NUM       4
  #define VSYNC_GPIO_NUM   25
  #define HREF_GPIO_NUM    23
  #define PCLK_GPIO_NUM    22

#elif defined(CAMERA_MODEL_M5STACK_PSRAM)
  #define PWDN_GPIO_NUM     -1
  #define RESET_GPIO_NUM    15
  #define XCLK_GPIO_NUM     27
  #define SIOD_GPIO_NUM     25
  #define SIOC_GPIO_NUM     23
  
  #define Y9_GPIO_NUM       19
  #define Y8_GPIO_NUM       36
  #define Y7_GPIO_NUM       18
  #define Y6_GPIO_NUM       39
  #define Y5_GPIO_NUM        5
  #define Y4_GPIO_NUM       34
  #define Y3_GPIO_NUM       35
  #define Y2_GPIO_NUM       32
  #define VSYNC_GPIO_NUM    22
  #define HREF_GPIO_NUM     26
  #define PCLK_GPIO_NUM     21

#elif defined(CAMERA_MODEL_M5STACK_WITHOUT_PSRAM)
  #define PWDN_GPIO_NUM     -1
  #define RESET_GPIO_NUM    15
  #define XCLK_GPIO_NUM     27
  #define SIOD_GPIO_NUM     25
  #define SIOC_GPIO_NUM     23
  
  #define Y9_GPIO_NUM       19
  #define Y8_GPIO_NUM       36
  #define Y7_GPIO_NUM       18
  #define Y6_GPIO_NUM       39
  #define Y5_GPIO_NUM        5
  #define Y4_GPIO_NUM       34
  #define Y3_GPIO_NUM       35
  #define Y2_GPIO_NUM       17
  #define VSYNC_GPIO_NUM    22
  #define HREF_GPIO_NUM     26
  #define PCLK_GPIO_NUM     21

#elif defined(CAMERA_MODEL_AI_THINKER)
  #define PWDN_GPIO_NUM     32
  #define RESET_GPIO_NUM    -1
  #define XCLK_GPIO_NUM      0
  #define SIOD_GPIO_NUM     26
  #define SIOC_GPIO_NUM     27
  
  #define Y9_GPIO_NUM       35
  #define Y8_GPIO_NUM       34
  #define Y7_GPIO_NUM       39
  #define Y6_GPIO_NUM       36
  #define Y5_GPIO_NUM       21
  #define Y4_GPIO_NUM       19
  #define Y3_GPIO_NUM       18
  #define Y2_GPIO_NUM        5
  #define VSYNC_GPIO_NUM    25
  #define HREF_GPIO_NUM     23
  #define PCLK_GPIO_NUM     22

#elif defined(CAMERA_MODEL_M5STACK_PSRAM_B)
  #define PWDN_GPIO_NUM     -1
  #define RESET_GPIO_NUM    15
  #define XCLK_GPIO_NUM     27
  #define SIOD_GPIO_NUM     22
  #define SIOC_GPIO_NUM     23
  
  #define Y9_GPIO_NUM       19
  #define Y8_GPIO_NUM       36
  #define Y7_GPIO_NUM       18
  #define Y6_GPIO_NUM       39
  #define Y5_GPIO_NUM        5
  #define Y4_GPIO_NUM       34
  #define Y3_GPIO_NUM       35
  #define Y2_GPIO_NUM       32
  #define VSYNC_GPIO_NUM    25
  #define HREF_GPIO_NUM     26
  #define PCLK_GPIO_NUM     21

#else
  #error "Camera model not selected"
#endif

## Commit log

2026-02-23 More adjustments to Webseite, added servo control
2026-03-23 Fixed camera lag issues
    [pllcalc.ods]
2026-03-28 servo update
2026-03-28 servo optimiert
2026-04-13 Add PCB dev (not finished)
    [motordriver.kicad_pcb, motordriver.kicad_sch]
2026-05-24 PCB created
    [BOM-motordriver.csv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]
2026-05-26 Updated PCB, fixed minor bugs on PCB
    [BOM-motordriver.csv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]
2026-06-07 Under the hood adjustments, on-screen buttons still missing...
    [Car_Robot_Camera_Web_Server.ino, PwmThing.cpp, PwmThing.h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]
2026-06-08 Buttons working
2026-06-11 Quite good
    [robi_min_spiffs.csv]
